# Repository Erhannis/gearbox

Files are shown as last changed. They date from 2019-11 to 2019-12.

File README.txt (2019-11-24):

OpenSCAD planetary gearbox.  Repo at https://github.com/Erhannis/gearbox .  A port of one of Gear Down For What's gearboxes: https://www.thingiverse.com/thing:2054378 .  His is licensed under CC/A/SA ; I don't know what that makes mine.  Mine is otherwise MIT licensed.

Run get_deps.sh to get the dependencies from github.  If you're running windows, install git, make a "deps.link" folder where you have the gearbox scad, then in that folder run the "git clone" lines of the "get_deps.sh" file.  OpenSCAD should be able to read gearbox.scad properly, then.

Oh, and flattedShaft is just a test crank.  Didn't have anything around that fit quite like a stepper motor shaft.  (If anybody knows where to buy 2.5mm radius D-shaped shafts like that, I'd be interested in buying some, btw.)

Printing: I used 0.2 layer height, 20% infill.  Cura's "Standard Quality" setting.  (Skirt, not brim.)  BUT, by default it's far too tight a fit.  I've discovered that Cura's "Horizontal Expansion" setting sorta makes it as if you dipped your piece in wax or in acid, for positive and negative values, respectively; it's pretty great as an "auto-tolerance" setting.  I found between -0.08 (slightly too tight) and -0.1 (slightly too loose) to be good on my printer.  Note that if you aren't careful, Horizontal Expansion can eat through pieces if they were already thin and you set it too high (negative).

Assembly: use GDFW's instructions.  The orientation of the planet gears is very important - two adjacent facing the same direction, the other two facing the opposite direction.

-Erhannis

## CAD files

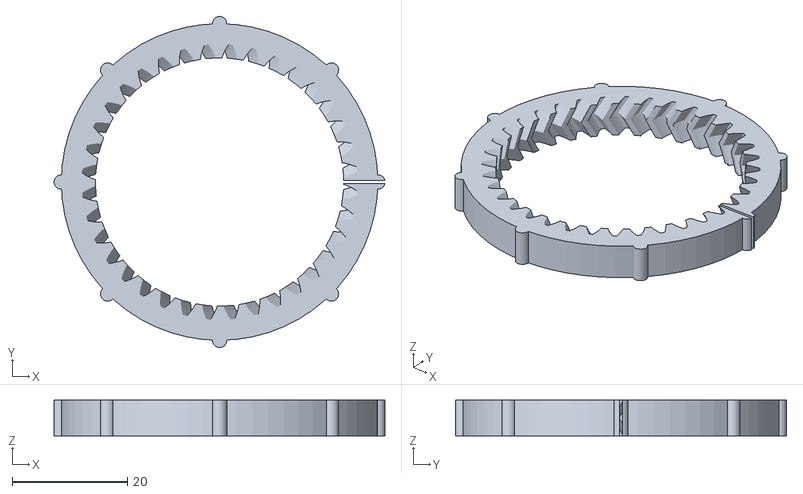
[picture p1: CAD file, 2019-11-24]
small_ring.stl
57.5 x 57.5 x 6.25

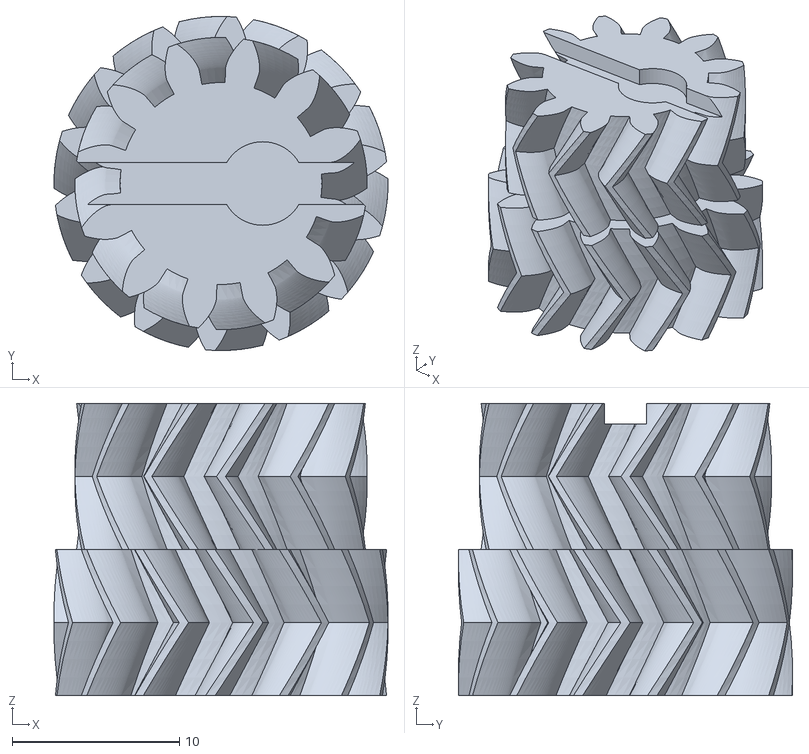
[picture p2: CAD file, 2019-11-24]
shaft.stl
20.0 x 20.0 x 17.5

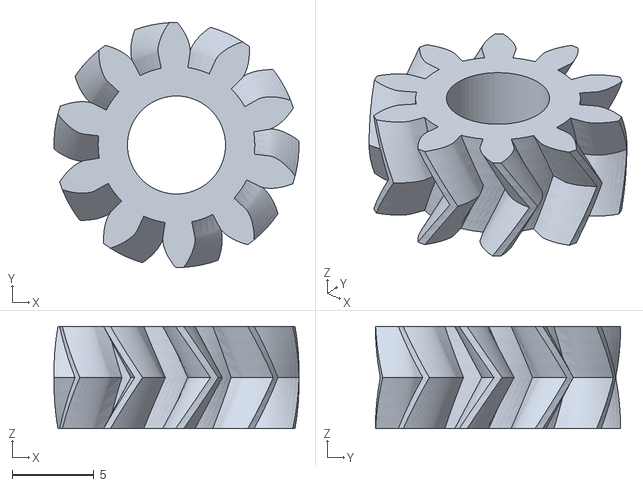
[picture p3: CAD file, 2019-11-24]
small_sun.stl
15.0 x 15.0 x 6.25

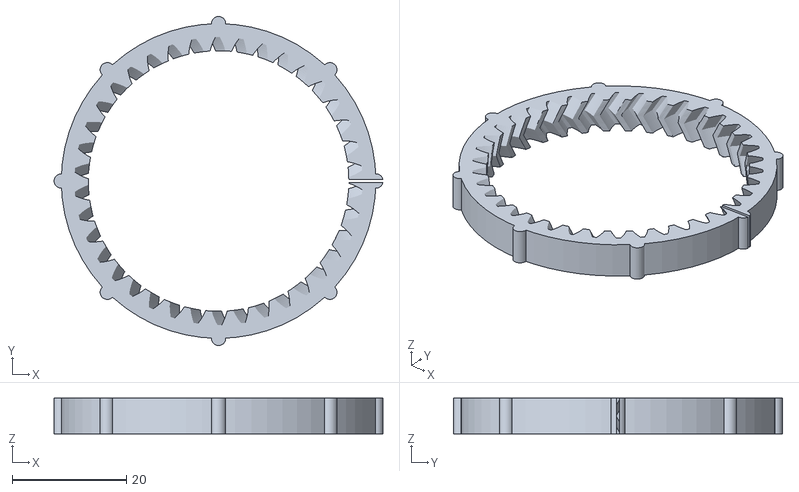
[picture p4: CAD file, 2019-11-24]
large_ring.stl
57.5 x 57.5 x 6.25

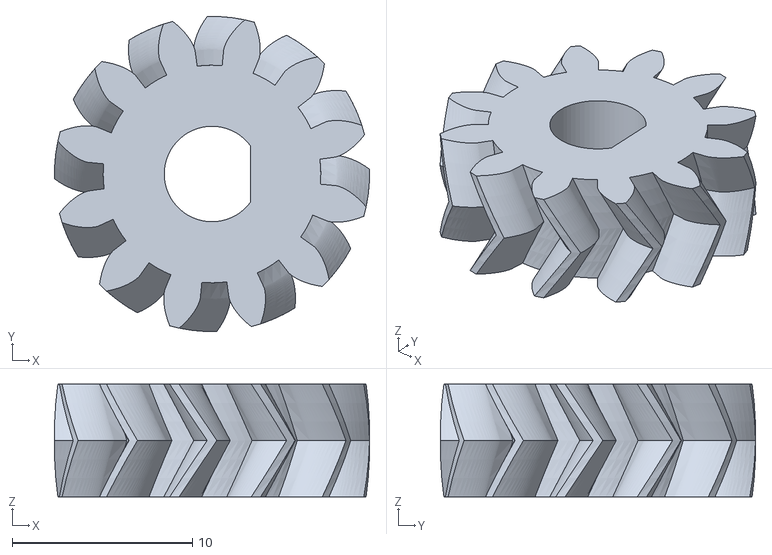
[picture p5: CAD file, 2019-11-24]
large_sun.stl
17.5 x 17.5 x 6.25

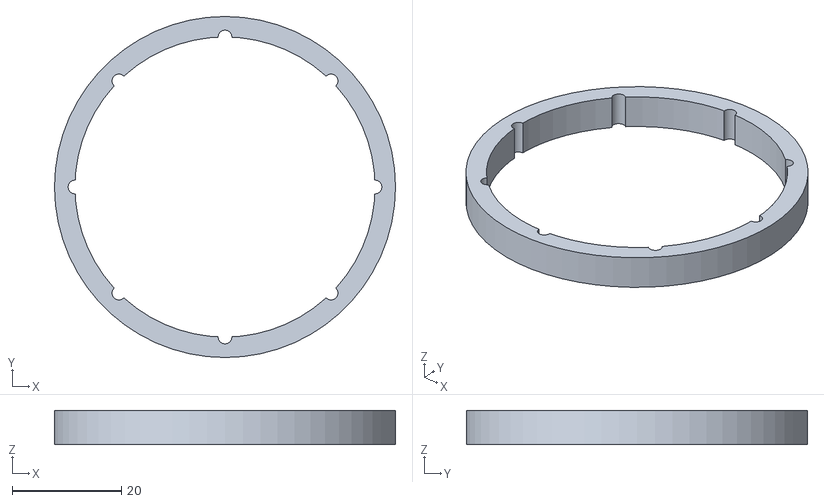
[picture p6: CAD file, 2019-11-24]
sheath.stl
62.5 x 62.5 x 6.25

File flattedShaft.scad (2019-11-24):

use <deps.link/erhannisScad/misc.scad>
use <deps.link/getriebe/Getriebe.scad>

$fn=60;
$BIG = 1000;

flattedShaft(h=30,r=2.5);
pfeilrad(modul=4, zahnzahl=7, breite=5, bohrung=0, eingriffswinkel=25, schraegungswinkel=30, optimiert=false);

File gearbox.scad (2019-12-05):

use <deps.link/erhannisScad/misc.scad>
use <deps.link/getriebe/Getriebe.scad>

/**
I recommend printing all these with
Horizontal Expansion: -0.08
Initial Layer Horizontal Expansion: -0.3

Otherwise they are way too tight to even fit together.
*/

/**
If smallSun(drive=true), then the gear ratio is higher than if largeSun(drive=true).
(Only one should drive, or you get a crash.  Haha.)
*/

$fn=60;
$BIG = 1000;

SZ = 5;
SZ_GAP = 2;

IND_W = 2;
IND_D = 2;

RING_D = 44;
SHEATH_W = 6;
GROOVE_D = 2;
CUT_W = 0.5;
SCALE = 5/4;

BIG_FACTOR = 4;

// 36 ring, 12 shaft, 12 sun
// 38 ring, 14 shaft, 10 sun

//TODO I should probably parameterize these modules at some point

module grooves(big=false) {
    bf = big ? BIG_FACTOR : 1;
    for (i = [1:8]) {
        rotate([0,0,i*45])
            translate([RING_D/2,0,0])
            cylinder(d=GROOVE_D,h=SZ*bf);
    }
}

module smallRing(big=false) {
    bf = big ? BIG_FACTOR : 1;
    difference() {
        scale(SCALE) union() { // Small ring (36)
            if (big) {
                for (i = [0:BIG_FACTOR-1]) {
                    translate([0,0,i*SZ])
                        pfeilhohlrad(modul=1, zahnzahl=36, breite=SZ, randbreite=0.1, eingriffswinkel=20, schraegungswinkel=30);
                }
            } else {
                pfeilhohlrad(modul=1, zahnzahl=36, breite=SZ, randbreite=0.1, eingriffswinkel=20, schraegungswinkel=30);
            }
            dims = pfeilhohlrad_dims(modul=1, zahnzahl=36, breite=SZ, randbreite=0.1, eingriffswinkel=20, schraegungswinkel=30);
            difference() {
                cylinder(d=RING_D, h=SZ*bf);
                cylinder(d=dims[1], h=SZ*bf);
            }
            grooves(big=big);
        }
        translate([0,-CUT_W/2,0]) cube([$BIG,CUT_W,$BIG]);
    }
}

module largeRing(big=false) {
    bf = big ? BIG_FACTOR : 1;
    difference() {
        scale(SCALE) union() { // Large ring (38)
            if (big) {
                for (i = [0:BIG_FACTOR-1]) {
                    translate([0,0,i*SZ])
                        pfeilhohlrad(modul=1, zahnzahl=38, breite=SZ, randbreite=0.1, eingriffswinkel=20, schraegungswinkel=30);
                }
            } else {
                pfeilhohlrad(modul=1, zahnzahl=38, breite=SZ, randbreite=0.1, eingriffswinkel=20, schraegungswinkel=30);
            }
            dims = pfeilhohlrad_dims(modul=1, zahnzahl=38, breite=SZ, randbreite=0.1, eingriffswinkel=20, schraegungswinkel=30);
            difference() {
                cylinder(d=RING_D, h=SZ*bf);
                cylinder(d=dims[1], h=SZ*bf);
            }
            grooves(big=big);
        }
        translate([0,-CUT_W/2,0]) cube([$BIG,CUT_W,$BIG]);
    }
}

module sheath(big=false) {
    bf = big ? BIG_FACTOR : 1;
    scale(SCALE) difference() { // Sheath ; print 2 of these
        cylinder(d=RING_D+SHEATH_W,h=SZ*bf);
        cylinder(d=RING_D,h=SZ*bf);
        grooves(big=big);
    }
}

module shaft(small_big=false, big_big=false) {
    sbf = small_big ? BIG_FACTOR : 1;
    bbf = big_big ? BIG_FACTOR : 1;
    scale(SCALE) difference() { // Shaft 14/12 ; print 4 of these
        union() {
            if (big_big) {
                difference() {
                    pfeilrad(modul=1, zahnzahl=14, breite=SZ+SZ_GAP, bohrung=0, eingriffswinkel=20, schraegungswinkel=30, optimiert=false);
                    OZp([0,0,SZ+SZ_GAP/2]);
                }
                for (i = [1:1:BIG_FACTOR-2]) {
                    translate([0,0,SZ*i+SZ_GAP/2])
                        pfeilrad(modul=1, zahnzahl=14, breite=SZ, bohrung=0, eingriffswinkel=20, schraegungswinkel=30, optimiert=false);
                }
                translate([0,0,SZ*(BIG_FACTOR-1)+SZ_GAP/2]) difference() {
                    translate([0,0,-SZ_GAP/2]) pfeilrad(modul=1, zahnzahl=14, breite=SZ+SZ_GAP, bohrung=0, eingriffswinkel=20, schraegungswinkel=30, optimiert=false);
                    OZm();
                }
            } else {
                pfeilrad(modul=1, zahnzahl=14, breite=SZ+SZ_GAP, bohrung=0, eingriffswinkel=20, schraegungswinkel=30, optimiert=false);
            }
            if (small_big) {
                translate([0,0,SZ*bbf+SZ_GAP]) {
                    difference() {
                        pfeilrad(modul=1, zahnzahl=12, breite=SZ+SZ_GAP, bohrung=0, eingriffswinkel=20, schraegungswinkel=-30, optimiert=false);
                        OZp([0,0,SZ+SZ_GAP/2]);
                    }
                    for (i = [1:1:BIG_FACTOR-2]) {
                        translate([0,0,SZ*i+SZ_GAP/2])
                            pfeilrad(modul=1, zahnzahl=12, breite=SZ, bohrung=0, eingriffswinkel=20, schraegungswinkel=-30, optimiert=false);
                    }
                    translate([0,0,SZ*(BIG_FACTOR-1)+SZ_GAP/2]) difference() {
                        translate([0,0,-SZ_GAP/2]) pfeilrad(modul=1, zahnzahl=12, breite=SZ+SZ_GAP, bohrung=0, eingriffswinkel=20, schraegungswinkel=-30, optimiert=false);
                        OZm();
                    }
                }
            } else {
                translate([0,0,SZ*bbf+SZ_GAP]) pfeilrad(modul=1, zahnzahl=12, breite=SZ+SZ_GAP, bohrung=0, eingriffswinkel=20, schraegungswinkel=-30, optimiert=false);
            }
        }
        translate([0,0,(SZ*sbf+SZ_GAP)+(SZ*bbf+SZ_GAP)]) {
            cube([$BIG, IND_W, IND_D], center=true);
            translate([IND_W,0,0]) cylinder(d=2*IND_W,h=IND_D, center=true);
        }
    }
}

module smallSun(drive=true, big=false) {
    difference() {
        scale(SCALE) union() { // Small sun (10)
            if (big) {
                pfeilrad(modul=1, zahnzahl=10, breite=SZ, bohrung=0, eingriffswinkel=20, schraegungswinkel=30, optimiert=false);
                for (i = [1:1:BIG_FACTOR-2]) {
                    translate([0,0,SZ*i])
                        pfeilrad(modul=1, zahnzahl=10, breite=SZ, bohrung=0, eingriffswinkel=20, schraegungswinkel=30, optimiert=false);
                }
                translate([0,0,SZ*(BIG_FACTOR-1)])
                    pfeilrad(modul=1, zahnzahl=10, breite=SZ, bohrung=0, eingriffswinkel=20, schraegungswinkel=30, optimiert=false);
            } else {
                pfeilrad(modul=1, zahnzahl=10, breite=SZ, bohrung=0, eingriffswinkel=20, schraegungswinkel=30, optimiert=false);
            }
        }
        if (drive) {
            flattedShaft(h=$BIG,r=2.5 + 0.15,center=true);
        } else {
            cylinder(h=$BIG,r=2.7,center=true);
        }
    }
}

module largeSun(drive=false, big=false) {
    difference() {
        scale(SCALE) union() { // Large sun (12)
            if (big) {
                pfeilrad(modul=1, zahnzahl=12, breite=SZ, bohrung=0, eingriffswinkel=20, schraegungswinkel=30, optimiert=false);
                for (i = [1:1:BIG_FACTOR-2]) {
                    translate([0,0,SZ*i])
                        pfeilrad(modul=1, zahnzahl=12, breite=SZ, bohrung=0, eingriffswinkel=20, schraegungswinkel=30, optimiert=false);
                }
                translate([0,0,SZ*(BIG_FACTOR-1)])
                    pfeilrad(modul=1, zahnzahl=12, breite=SZ, bohrung=0, eingriffswinkel=20, schraegungswinkel=30, optimiert=false);
            } else {
                pfeilrad(modul=1, zahnzahl=12, breite=SZ, bohrung=0, eingriffswinkel=20, schraegungswinkel=30, optimiert=false);
            }
        }
        if (drive) {
            flattedShaft(h=$BIG,r=2.5 + 0.15,center=true);
        } else {
            cylinder(h=$BIG,r=2.7,center=true);
        }
    }
}

* smallRing();
* largeRing();
* sheath();
* shaft();
* smallSun();
* largeSun();

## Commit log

2019-11-24 Initial commit. OpenSCAD port of one of Gear Down For What's 3d printed gearboxes.
    [flattedShaft.scad, gearbox.scad, large_ring.stl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]
2019-11-24 Added assembly to readme.
2019-11-26 Turned things into modules, to work better as a dependency. Should probably parameterize them eventually.
    [gearbox.scad]
2019-11-29 Added option for which sun gear should drive.
    [gearbox.scad]
2019-11-30 Mentioned horiz expansion in scad file
    [gearbox.scad]
2019-12-05 Added the ability to make gears wider, for (presumable) added strength.
    [gearbox.scad]
